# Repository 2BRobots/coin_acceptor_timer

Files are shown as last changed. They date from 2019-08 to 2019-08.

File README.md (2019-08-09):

# Coin Acceptor Timer module for Vending Machines

The timer must be powered with regulated 12 VDC. When there is electric power, the POWER LED will remain lit as the power present indicator and the STAT LED will light momentarily once. Whenever the timer is enabled, the RELAY LED will illuminate while the timer remains active. When a pulse is received from the coin acceptor, the STAT LED will flash rapidly for each pulse received (credit), the pulses are always counted regardless of the timer is active or not.

The pulse input from the coin acceptor in the timer is open collector type. Which means that the coin acceptor must send a low logic signal (GND) every time it sends a credit and in standby state it must be floating (no voltage). The pulses must have a minimum width of 10 ms and a separation of 5 ms between pulses.

The timer is programmed to disable the relay between each transaction, if you need it to be constantly enabled while it has enough credits please contact us for customization.

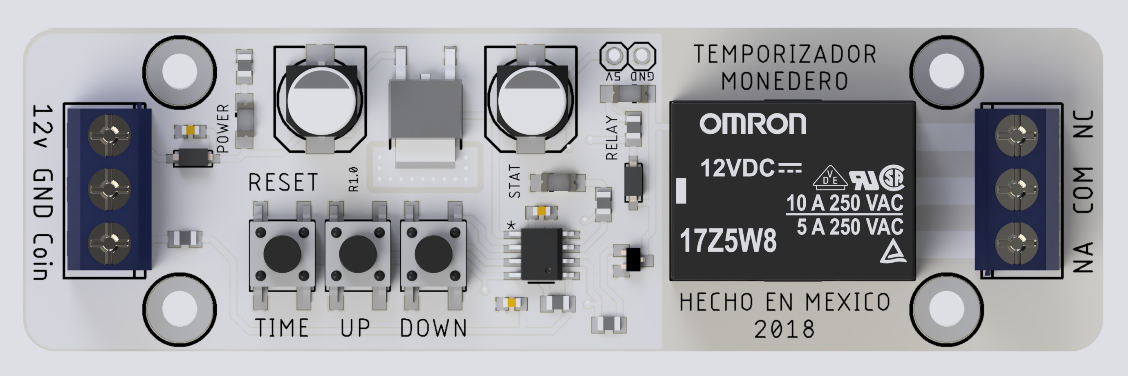
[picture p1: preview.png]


How to modify the settings:

1. To change the number of pulses (credits) with which the timer is activated press the UP and DOWN buttons. With UP it increases and with DOWN it decreases, each time the setting is changed the STAT LED will flash rapidly. When the upper or lower limit is reached, the STAT LED flash slowly.

2. To change the time (seconds) that the timer is enabled, the procedure is the same as the previous one, exept you must keep the TIME / RESET button pressed while pressing UP and DOWN.

3. To reset the timer to factory settings, press and hold the TIME / RESET button when the timer is turned on. The STAT LED will flash rapidly 2 times indicating that the restart was successful. Default values are 1 credit for 5 seconds.

Note: the maximum value for both cases (time and credits) is 100 and the minimum is 1.
The timer does not lose its settings when it is turned on and off.

You can purchase this module on Tindie: https://www.tindie.com/products/Danny024/timer-module-for-vending-machine/

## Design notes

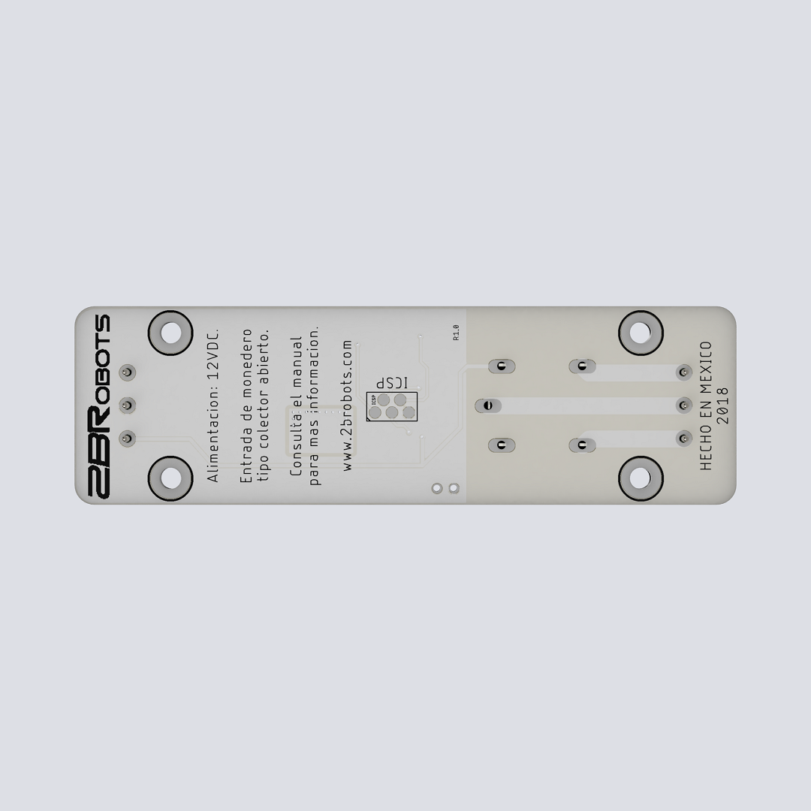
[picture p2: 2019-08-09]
Renders/botton_render.png

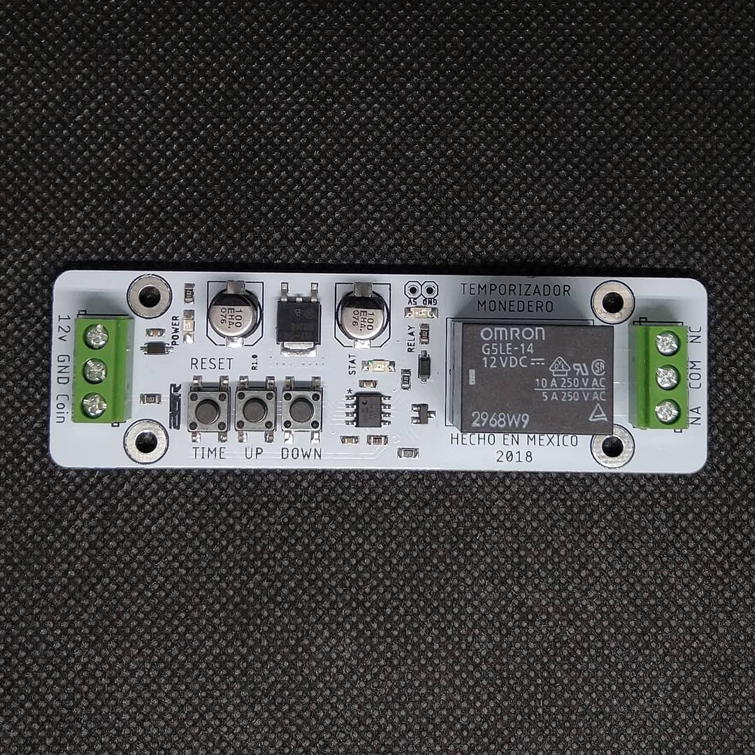
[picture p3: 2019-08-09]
Renders/top_real.jpg

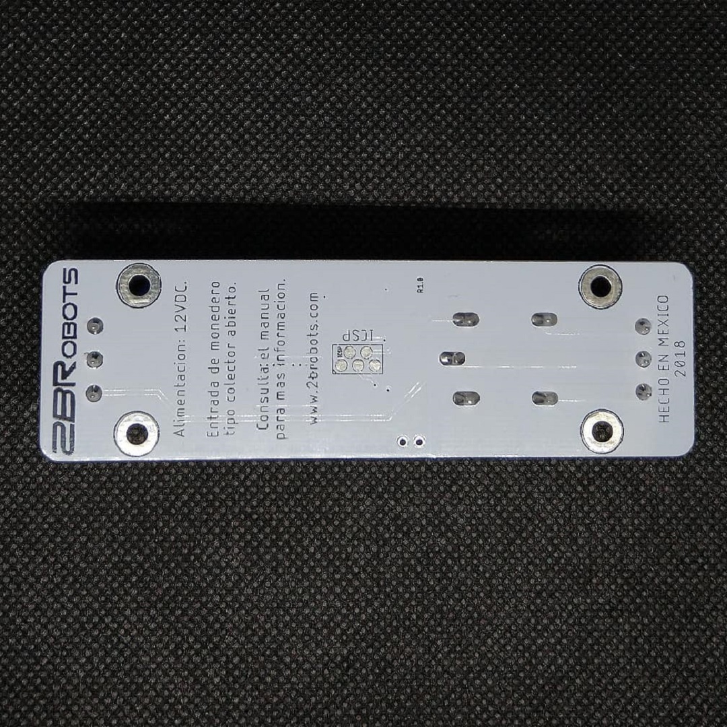
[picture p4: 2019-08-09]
Renders/botton_real.jpg

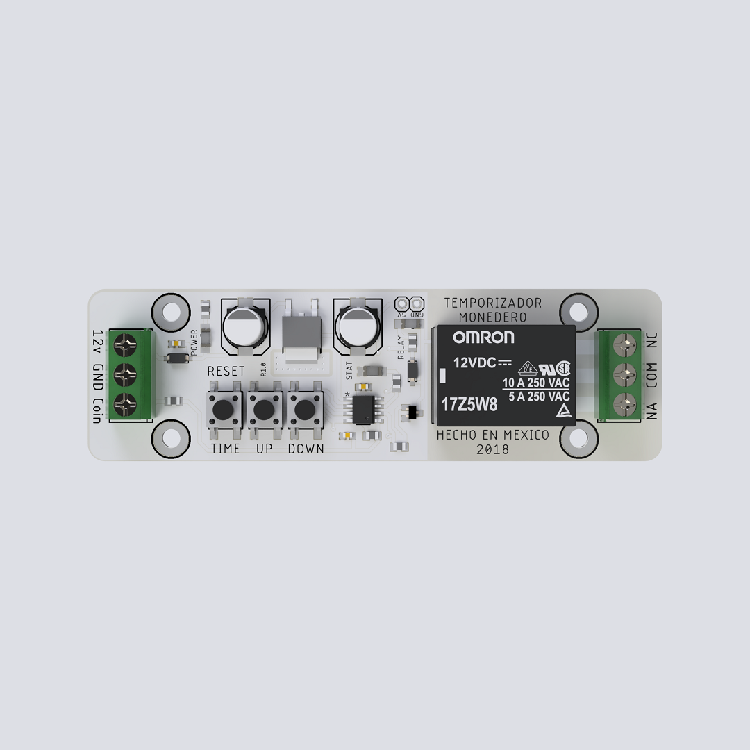
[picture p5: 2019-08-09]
Renders/top-render.png

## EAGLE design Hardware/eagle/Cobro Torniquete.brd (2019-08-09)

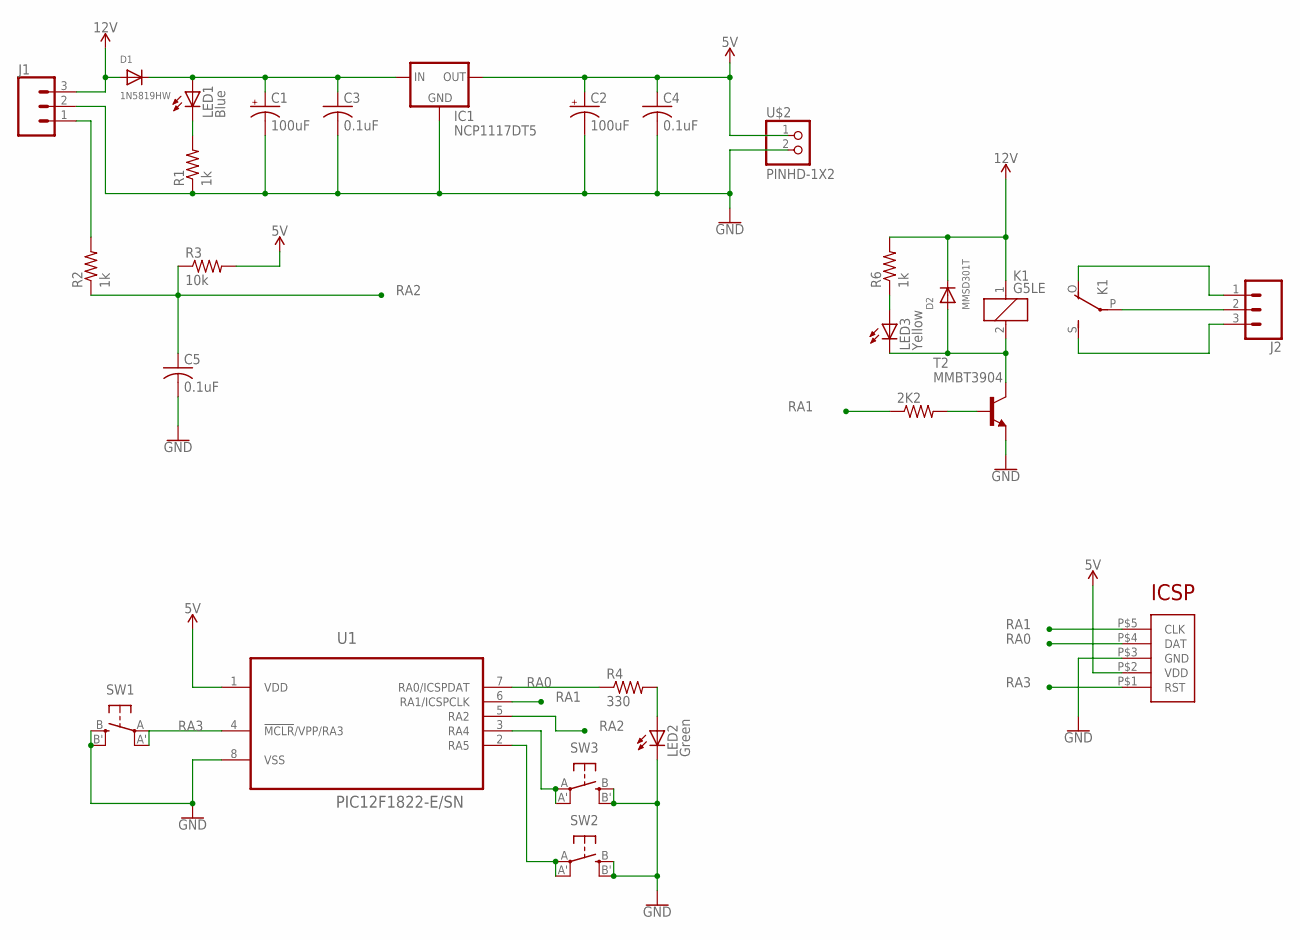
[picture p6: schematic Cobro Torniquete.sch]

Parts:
2K2: R-US_R0805; R0805
C1, C2: 100uF; 140CLH-0810
C3, C4, C5: 0.1uF; C0603K
D1: 1N5819HW; SOD-123
D2: MMSD301T; SOD-123
IC1: NCP1117DT5; TO252
J1, J2: CONN_03-SCREW-5MM; SCREWTERMINAL-5MM-3
K1: G5LE
LED1: Blue; CHIPLED_1206
LED2: Green; CHIPLED_1206
LED3: Yellow; CHIPLED_1206
R1, R2, R6: 1k; R0805
R3: 10k; R0805
R4: 330; R0805
SW1, SW2, SW3: SPST_TACT-EVQQ2; EVQ-Q2
T2: MMBT3904; SOT23-BEC
U1: PIC12F1822-E/SN; SOIC127P600X175-8N
U$1: ICSP_POGO
U$2: PINHD-1X2; 1X2

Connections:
5V: C2.+, C4.1, IC1.3 (OUT), R3.2, U1.1 (VDD), U$1.P$2 (VDD), U$2.1
12V: D1.A, D2.C, J1.3, K1.1, R6.2
GND: C1.-, C2.-, C3.2, C4.2, C5.2, IC1.1 (GND), J1.2, LED2.C, R1.1, SW1.B (S), SW1.B' (S1), SW2.B (S), SW2.B' (S1), SW3.B (S), SW3.B' (S1), T2.E, U1.8 (VSS), U$1.P$3 (GND), U$2.2
unnamed: C1.+, C3.1, D1.C, IC1.2 (IN), LED1.A
unnamed: LED1.C, R1.2
unnamed: J2.2, K1.P
unnamed: J1.1, R2.2
unnamed: J2.3, K1.S
unnamed: J2.1, K1.O
unnamed: D2.A, K1.2, LED3.C, T2.C
unnamed: LED2.A, R4.2
unnamed: LED3.A, R6.1
unnamed: 2K2.2, T2.B
unnamed: SW3.A, SW3.A' (P1), U1.3 (RA4)
unnamed: SW2.A, SW2.A' (P1), U1.2 (RA5)
RA0: R4.1, U1.7 (RA0/ICSPDAT), U$1.P$4 (DAT)
RA1: 2K2.1, U1.6 (RA1/ICSPCLK), U$1.P$5 (CLK)
RA2: C5.1, R2.1, R3.1, U1.5 (RA2)
RA3: SW1.A, SW1.A' (P1), U1.4 (!MCLR!/VPP/RA3), U$1.P$1 (RST)

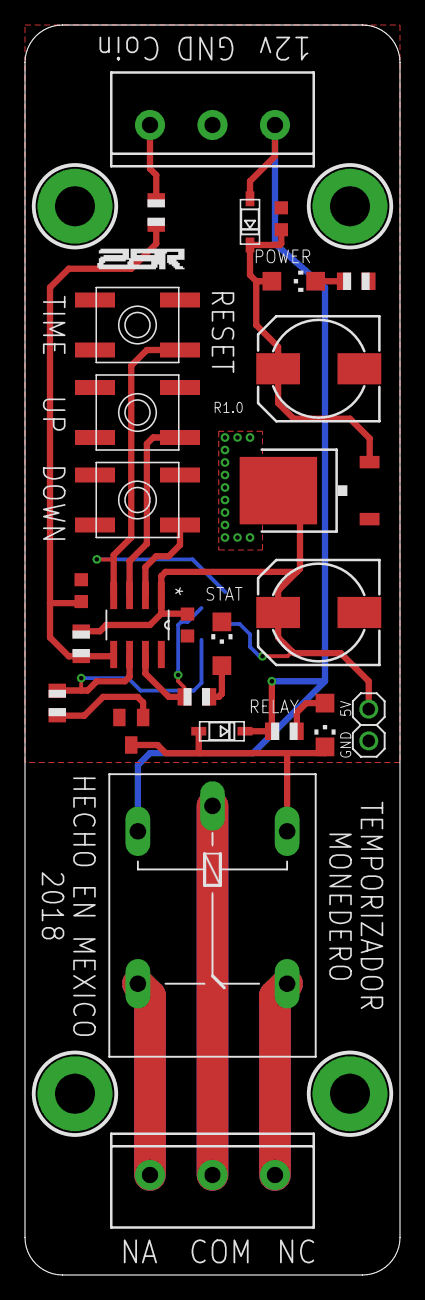
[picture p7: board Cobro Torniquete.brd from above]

Board: 2 copper layers, 30.0 x 100.0 mm, 27 parts (1 on the bottom side), 19 nets.

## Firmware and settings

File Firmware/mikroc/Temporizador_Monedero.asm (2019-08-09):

_interrupt:

;Temporizador_Monedero.c,20 :: 		void interrupt() iv 0x0004 ics ICS_AUTO //interrupts
;Temporizador_Monedero.c,22 :: 		if (INTCON.f1 == 1) //interrupt on change on RA4 triggered
	BTFSS      INTCON+0, 1
	GOTO       L_interrupt0
;Temporizador_Monedero.c,24 :: 		INTCON.f7 = 0; //stop interrupts
	BCF        INTCON+0, 7
;Temporizador_Monedero.c,25 :: 		delay_ms(10);
	MOVLW      104
	MOVWF      R12
	MOVLW      228
	MOVWF      R13
L_interrupt1:
	DECFSZ     R13, 1
	GOTO       L_interrupt1
	DECFSZ     R12, 1
	GOTO       L_interrupt1
	NOP
;Temporizador_Monedero.c,26 :: 		if (COIN == 0)
	BTFSC      PORTA+0, 2
	GOTO       L_interrupt2
;Temporizador_Monedero.c,28 :: 		LED = 1;
	BSF        PORTA+0, 0
;Temporizador_Monedero.c,29 :: 		delay_ms(5);
	MOVLW      52
	MOVWF      R12
	MOVLW      241
	MOVWF      R13
L_interrupt3:
	DECFSZ     R13, 1
	GOTO       L_interrupt3
	DECFSZ     R12, 1
	GOTO       L_interrupt3
	NOP
	NOP
;Temporizador_Monedero.c,30 :: 		LED = 0;
	BCF        PORTA+0, 0
;Temporizador_Monedero.c,31 :: 		coins++;
	INCF       _coins+0, 1
;Temporizador_Monedero.c,32 :: 		}
L_interrupt2:
;Temporizador_Monedero.c,33 :: 		INTCON.f1 = 0; //clear interrupt flags
	BCF        INTCON+0, 1
;Temporizador_Monedero.c,34 :: 		INTCON.f7 = 1; //run interrupts
	BSF        INTCON+0, 7
;Temporizador_Monedero.c,35 :: 		}
L_interrupt0:
;Temporizador_Monedero.c,36 :: 		}
L_end_interrupt:
L__interrupt75:
	RETFIE     %s
; end of _interrupt

_main:

;Temporizador_Monedero.c,38 :: 		void main()
;Temporizador_Monedero.c,40 :: 		OSCCON = 0b11110000; //configure internal oscilator for 32Mhz
	MOVLW      240
	MOVWF      OSCCON+0
;Temporizador_Monedero.c,41 :: 		TRISA = 0b00111100;  //configure IO
	MOVLW      60
	MOVWF      TRISA+0
;Temporizador_Monedero.c,42 :: 		ANSELA = 0b00000000; //analog functions of pins disabled
	CLRF       ANSELA+0
;Temporizador_Monedero.c,43 :: 		WPUA = 0b00111100;   //configure weak pull-ups on input pins
	MOVLW      60
	MOVWF      WPUA+0
;Temporizador_Monedero.c,44 :: 		PORTA = 0b0000000;
	CLRF       PORTA+0
;Temporizador_Monedero.c,45 :: 		OPTION_REG.f7 = 0;   //enable weak pull-ups
	BCF        OPTION_REG+0, 7
;Temporizador_Monedero.c,46 :: 		OPTION_REG.f6 = 0; //interrupt on falling edge
	BCF        OPTION_REG+0, 6
;Temporizador_Monedero.c,47 :: 		INTCON = 0b00010000; //enables interrupts
	MOVLW      16
	MOVWF      INTCON+0
;Temporizador_Monedero.c,48 :: 		if (BT_TIME == 1)
	BTFSS      PORTA+0, 3
	GOTO       L_main4
;Temporizador_Monedero.c,50 :: 		price = EEPROM_read(0);
	CLRF       FARG_EEPROM_Read_Address+0
	CALL       _EEPROM_Read+0
	MOVF       R0, 0
	MOVWF      _price+0
;Temporizador_Monedero.c,51 :: 		time = EEPROM_read(1);
	MOVLW      1
	MOVWF      FARG_EEPROM_Read_Address+0
	CALL       _EEPROM_Read+0
	MOVF       R0, 0
	MOVWF      _time+0
;Temporizador_Monedero.c,52 :: 		LED = 1;
	BSF        PORTA+0, 0
;Temporizador_Monedero.c,53 :: 		delay_ms(250);
	MOVLW      11
	MOVWF      R11
	MOVLW      38
	MOVWF      R12
	MOVLW      93
	MOVWF      R13
L_main5:
	DECFSZ     R13, 1
	GOTO       L_main5
	DECFSZ     R12, 1
	GOTO       L_main5
	DECFSZ     R11, 1
	GOTO       L_main5
	NOP
	NOP
;Temporizador_Monedero.c,54 :: 		LED = 0;
	BCF        PORTA+0, 0
;Temporizador_Monedero.c,55 :: 		}
	GOTO       L_main6
L_main4:
;Temporizador_Monedero.c,58 :: 		price = default_price;
	MOVLW      1
	MOVWF      _price+0
;Temporizador_Monedero.c,59 :: 		time = default_time;
	MOVLW      5
	MOVWF      _time+0
;Temporizador_Monedero.c,60 :: 		EEPROM_write(0,price);
	CLRF       FARG_EEPROM_Write_Address+0
	MOVLW      1
	MOVWF      FARG_EEPROM_Write_data_+0
	CALL       _EEPROM_Write+0
;Temporizador_Monedero.c,61 :: 		EEPROM_write(1,time);
	MOVLW      1
	MOVWF      FARG_EEPROM_Write_Address+0
	MOVF       _time+0, 0
	MOVWF      FARG_EEPROM_Write_data_+0
	CALL       _EEPROM_Write+0
;Temporizador_Monedero.c,62 :: 		LED = 1;
	BSF        PORTA+0, 0
;Temporizador_Monedero.c,63 :: 		delay_ms(100);
	MOVLW      5
	MOVWF      R11
	MOVLW      15
	MOVWF      R12
	MOVLW      241
	MOVWF      R13
L_main7:
	DECFSZ     R13, 1
	GOTO       L_main7
	DECFSZ     R12, 1
	GOTO       L_main7
	DECFSZ     R11, 1
	GOTO       L_main7
;Temporizador_Monedero.c,64 :: 		LED = 0;
	BCF        PORTA+0, 0
;Temporizador_Monedero.c,65 :: 		delay_ms(50);
	MOVLW      3
	MOVWF      R11
	MOVLW      8
	MOVWF      R12
	MOVLW      119
	MOVWF      R13
L_main8:
	DECFSZ     R13, 1
	GOTO       L_main8
	DECFSZ     R12, 1
	GOTO       L_main8
	DECFSZ     R11, 1
	GOTO       L_main8
;Temporizador_Monedero.c,66 :: 		LED = 1;
	BSF        PORTA+0, 0
;Temporizador_Monedero.c,67 :: 		delay_ms(100);
	MOVLW      5
	MOVWF      R11
	MOVLW      15
	MOVWF      R12
	MOVLW      241
	MOVWF      R13
L_main9:
	DECFSZ     R13, 1
	GOTO       L_main9
	DECFSZ     R12, 1
	GOTO       L_main9
	DECFSZ     R11, 1
	GOTO       L_main9
;Temporizador_Monedero.c,68 :: 		LED = 0;
	BCF        PORTA+0, 0
;Temporizador_Monedero.c,69 :: 		}
L_main6:
;Temporizador_Monedero.c,70 :: 		INTCON.f7 = 1;       //run interrupts
	BSF        INTCON+0, 7
;Temporizador_Monedero.c,72 :: 		while(1)
L_main10:
;Temporizador_Monedero.c,74 :: 		if (coins >= price)
	MOVF       _price+0, 0
	SUBWF      _coins+0, 0
	BTFSS      STATUS+0, 0
	GOTO       L_main12
;Temporizador_Monedero.c,76 :: 		coins = coins - price;
	MOVF       _price+0, 0
	SUBWF      _coins+0, 1
;Temporizador_Monedero.c,77 :: 		RELAY = 1;
	BSF        PORTA+0, 1
;Temporizador_Monedero.c,78 :: 		Vdelay_ms(time*1000);
	MOVF       _time+0, 0
	MOVWF      R0
	CLRF       R1
	MOVLW      232
	MOVWF      R4
	MOVLW      3
	MOVWF      R5
	CALL       _Mul_16X16_U+0
	MOVF       R0, 0
	MOVWF      FARG_VDelay_ms_Time_ms+0
	MOVF       R1, 0
	MOVWF      FARG_VDelay_ms_Time_ms+1
	CALL       _VDelay_ms+0
;Temporizador_Monedero.c,79 :: 		RELAY = 0;
	BCF        PORTA+0, 1
;Temporizador_Monedero.c,80 :: 		delay_ms(spacing_time);
	MOVLW      61
	MOVWF      R11
	MOVLW      225
	MOVWF      R12
	MOVLW      63
	MOVWF      R13
L_main13:
	DECFSZ     R13, 1
	GOTO       L_main13
	DECFSZ     R12, 1
	GOTO       L_main13
	DECFSZ     R11, 1
	GOTO       L_main13
	NOP
	NOP
;Temporizador_Monedero.c,81 :: 		}
L_main12:
;Temporizador_Monedero.c,83 :: 		if(BT_TIME == 0 && BT_UP == 0 && BT_DOWN == 1)    //increment time
	BTFSC      PORTA+0, 3
	GOTO       L_main16
	BTFSC      PORTA+0, 4
	GOTO       L_main16
	BTFSS      PORTA+0, 5
	GOTO       L_main16
L__main73:
;Temporizador_Monedero.c,85 :: 		time++;
	INCF       _time+0, 1
;Temporizador_Monedero.c,86 :: 		if (time >= max_time)
	MOVLW      100
	SUBWF      _time+0, 0
	BTFSS      STATUS+0, 0
	GOTO       L_main17
;Temporizador_Monedero.c,88 :: 		time = max_time;
	MOVLW      100
	MOVWF      _time+0
;Temporizador_Monedero.c,89 :: 		LED = 1;
	BSF        PORTA+0, 0
;Temporizador_Monedero.c,90 :: 		delay_ms(200);
	MOVLW      9
	MOVWF      R11
	MOVLW      30
	MOVWF      R12
	MOVLW      228
	MOVWF      R13
L_main18:
	DECFSZ     R13, 1
	GOTO       L_main18
	DECFSZ     R12, 1
	GOTO       L_main18
	DECFSZ     R11, 1
	GOTO       L_main18
	NOP
;Temporizador_Monedero.c,91 :: 		LED = 0;
	BCF        PORTA+0, 0
;Temporizador_Monedero.c,92 :: 		}
	GOTO       L_main19
L_main17:
;Temporizador_Monedero.c,95 :: 		LED = 1;
	BSF        PORTA+0, 0
;Temporizador_Monedero.c,96 :: 		delay_ms(50);
	MOVLW      3
	MOVWF      R11
	MOVLW      8
	MOVWF      R12
	MOVLW      119
	MOVWF      R13
L_main20:
	DECFSZ     R13, 1
	GOTO       L_main20
	DECFSZ     R12, 1
	GOTO       L_main20
	DECFSZ     R11, 1
	GOTO       L_main20
;Temporizador_Monedero.c,97 :: 		LED = 0;
	BCF        PORTA+0, 0
;Temporizador_Monedero.c,98 :: 		}
L_main19:
;Temporizador_Monedero.c,99 :: 		EEPROM_write(1,time);
	MOVLW      1
	MOVWF      FARG_EEPROM_Write_Address+0
	MOVF       _time+0, 0
	MOVWF      FARG_EEPROM_Write_data_+0
	CALL       _EEPROM_Write+0
;Temporizador_Monedero.c,100 :: 		while(BT_TIME == 0 && BT_UP == 0 && BT_DOWN == 1)
L_main21:
	BTFSC      PORTA+0, 3
	GOTO       L_main22
	BTFSC      PORTA+0, 4
	GOTO       L_main22
	BTFSS      PORTA+0, 5
	GOTO       L_main22
L__main72:
;Temporizador_Monedero.c,102 :: 		delay_ms(10);
	MOVLW      104
	MOVWF      R12
	MOVLW      228
	MOVWF      R13
L_main25:
	DECFSZ     R13, 1
	GOTO       L_main25
	DECFSZ     R12, 1
	GOTO       L_main25
	NOP
;Temporizador_Monedero.c,103 :: 		}
	GOTO       L_main21
L_main22:
;Temporizador_Monedero.c,104 :: 		delay_ms(500);
	MOVLW      21
	MOVWF      R11
	MOVLW      75
	MOVWF      R12
	MOVLW      190
	MOVWF      R13
L_main26:
	DECFSZ     R13, 1
	GOTO       L_main26
	DECFSZ     R12, 1
	GOTO       L_main26
	DECFSZ     R11, 1
	GOTO       L_main26
	NOP
;Temporizador_Monedero.c,105 :: 		}
L_main16:
;Temporizador_Monedero.c,107 :: 		if(BT_TIME == 0 && BT_UP == 1 && BT_DOWN == 0)    //decrement time
	BTFSC      PORTA+0, 3
	GOTO       L_main29
	BTFSS      PORTA+0, 4
	GOTO       L_main29
	BTFSC      PORTA+0, 5
	GOTO       L_main29
L__main71:
;Temporizador_Monedero.c,109 :: 		time--;
	DECF       _time+0, 1
;Temporizador_Monedero.c,110 :: 		if (time <= min_time)
	MOVF       _time+0, 0
	SUBLW      1
	BTFSS      STATUS+0, 0
	GOTO       L_main30
;Temporizador_Monedero.c,112 :: 		time = min_time;
	MOVLW      1
	MOVWF      _time+0
;Temporizador_Monedero.c,113 :: 		LED = 1;
	BSF        PORTA+0, 0
;Temporizador_Monedero.c,114 :: 		delay_ms(200);
	MOVLW      9
	MOVWF      R11
	MOVLW      30
	MOVWF      R12
	MOVLW      228
	MOVWF      R13
L_main31:
	DECFSZ     R13, 1
	GOTO       L_main31
	DECFSZ     R12, 1
	GOTO       L_main31
	DECFSZ     R11, 1
	GOTO       L_main31
	NOP
;Temporizador_Monedero.c,115 :: 		LED = 0;
	BCF        PORTA+0, 0
;Temporizador_Monedero.c,116 :: 		}
	GOTO       L_main32
L_main30:
;Temporizador_Monedero.c,119 :: 		LED = 1;
	BSF        PORTA+0, 0
;Temporizador_Monedero.c,120 :: 		delay_ms(50);
	MOVLW      3
	MOVWF      R11
	MOVLW      8
	MOVWF      R12
	MOVLW      119
	MOVWF      R13
L_main33:
	DECFSZ     R13, 1
	GOTO       L_main33
	DECFSZ     R12, 1
	GOTO       L_main33
	DECFSZ     R11, 1
	GOTO       L_main33
;Temporizador_Monedero.c,121 :: 		LED = 0;
	BCF        PORTA+0, 0
;Temporizador_Monedero.c,122 :: 		}
L_main32:
;Temporizador_Monedero.c,123 :: 		EEPROM_write(1,time);
	MOVLW      1
	MOVWF      FARG_EEPROM_Write_Address+0
	MOVF       _time+0, 0
	MOVWF      FARG_EEPROM_Write_data_+0
	CALL       _EEPROM_Write+0
;Temporizador_Monedero.c,124 :: 		while(BT_TIME == 0 && BT_UP == 1 && BT_DOWN == 0)
L_main34:
	BTFSC      PORTA+0, 3
	GOTO       L_main35
	BTFSS      PORTA+0, 4
	GOTO       L_main35
	BTFSC      PORTA+0, 5
	GOTO       L_main35
L__main70:
;Temporizador_Monedero.c,126 :: 		delay_ms(10);
	MOVLW      104
	MOVWF      R12
	MOVLW      228
	MOVWF      R13
L_main38:
	DECFSZ     R13, 1
	GOTO       L_main38
	DECFSZ     R12, 1
	GOTO       L_main38
	NOP
;Temporizador_Monedero.c,127 :: 		}
	GOTO       L_main34
L_main35:
;Temporizador_Monedero.c,128 :: 		delay_ms(500);
	MOVLW      21
	MOVWF      R11
	MOVLW      75
	MOVWF      R12
	MOVLW      190
	MOVWF      R13
L_main39:
	DECFSZ     R13, 1
	GOTO       L_main39
	DECFSZ     R12, 1
	GOTO       L_main39
	DECFSZ     R11, 1
	GOTO       L_main39
	NOP
;Temporizador_Monedero.c,129 :: 		}
L_main29:
;Temporizador_Monedero.c,131 :: 		if(BT_TIME == 1 && BT_UP == 0 && BT_DOWN == 1)    //increment price
	BTFSS      PORTA+0, 3
	GOTO       L_main42
	BTFSC      PORTA+0, 4
	GOTO       L_main42
	BTFSS      PORTA+0, 5
	GOTO       L_main42
L__main69:
;Temporizador_Monedero.c,133 :: 		price++;
	INCF       _price+0, 1
;Temporizador_Monedero.c,134 :: 		if (price >= max_price)
	MOVLW      100
	SUBWF      _price+0, 0
	BTFSS      STATUS+0, 0
	GOTO       L_main43
;Temporizador_Monedero.c,136 :: 		price = max_price;
	MOVLW      100
	MOVWF      _price+0
;Temporizador_Monedero.c,137 :: 		LED = 1;
	BSF        PORTA+0, 0
;Temporizador_Monedero.c,138 :: 		delay_ms(200);
	MOVLW      9
	MOVWF      R11
	MOVLW      30
	MOVWF      R12
	MOVLW      228
	MOVWF      R13
L_main44:
	DECFSZ     R13, 1
	GOTO       L_main44
	DECFSZ     R12, 1
	GOTO       L_main44
	DECFSZ     R11, 1
	GOTO       L_main44
	NOP
;Temporizador_Monedero.c,139 :: 		LED = 0;
	BCF        PORTA+0, 0
;Temporizador_Monedero.c,140 :: 		}
	GOTO       L_main45
L_main43:
;Temporizador_Monedero.c,143 :: 		LED = 1;
	BSF        PORTA+0, 0
;Temporizador_Monedero.c,144 :: 		delay_ms(50);
	MOVLW      3
	MOVWF      R11
	MOVLW      8
	MOVWF      R12
	MOVLW      119
	MOVWF      R13
L_main46:
	DECFSZ     R13, 1
	GOTO       L_main46
	DECFSZ     R12, 1
	GOTO       L_main46
	DECFSZ     R11, 1
	GOTO       L_main46
;Temporizador_Monedero.c,145 :: 		LED = 0;
	BCF        PORTA+0, 0
;Temporizador_Monedero.c,146 :: 		}
L_main45:
;Temporizador_Monedero.c,147 :: 		EEPROM_write(0,price);
	CLRF       FARG_EEPROM_Write_Address+0
	MOVF       _price+0, 0
	MOVWF      FARG_EEPROM_Write_data_+0
	CALL       _EEPROM_Write+0
;Temporizador_Monedero.c,148 :: 		while(BT_TIME == 1 && BT_UP == 0 && BT_DOWN == 1)
L_main47:
	BTFSS      PORTA+0, 3
	GOTO       L_main48
	BTFSC      PORTA+0, 4
	GOTO       L_main48
	BTFSS      PORTA+0, 5
	GOTO       L_main48
L__main68:
;Temporizador_Monedero.c,150 :: 		delay_ms(10);
	MOVLW      104
	MOVWF      R12
	MOVLW      228
	MOVWF      R13
L_main51:
	DECFSZ     R13, 1
	GOTO       L_main51
	DECFSZ     R12, 1
	GOTO       L_main51
	NOP
;Temporizador_Monedero.c,151 :: 		}
	GOTO       L_main47
L_main48:
;Temporizador_Monedero.c,152 :: 		delay_ms(500);
	MOVLW      21
	MOVWF      R11
	MOVLW      75
	MOVWF      R12
	MOVLW      190
	MOVWF      R13
L_main52:
	DECFSZ     R13, 1
	GOTO       L_main52
	DECFSZ     R12, 1
	GOTO       L_main52
	DECFSZ     R11, 1
	GOTO       L_main52
	NOP
;Temporizador_Monedero.c,153 :: 		}
L_main42:
;Temporizador_Monedero.c,155 :: 		if(BT_TIME == 1 && BT_UP == 1 && BT_DOWN == 0)    //decrement price
	BTFSS      PORTA+0, 3
	GOTO       L_main55
	BTFSS      PORTA+0, 4
	GOTO       L_main55
	BTFSC      PORTA+0, 5
	GOTO       L_main55
L__main67:
;Temporizador_Monedero.c,157 :: 		price--;
	DECF       _price+0, 1
;Temporizador_Monedero.c,158 :: 		if (price <= min_price)
	MOVF       _price+0, 0
	SUBLW      1
	BTFSS      STATUS+0, 0
	GOTO       L_main56
;Temporizador_Monedero.c,160 :: 		price = min_price;
	MOVLW      1
	MOVWF      _price+0
;Temporizador_Monedero.c,161 :: 		LED = 1;
	BSF        PORTA+0, 0
;Temporizador_Monedero.c,162 :: 		delay_ms(200);
	MOVLW      9
	MOVWF      R11
	MOVLW      30
	MOVWF      R12
	MOVLW      228
	MOVWF      R13
L_main57:
	DECFSZ     R13, 1
	GOTO       L_main57
	DECFSZ     R12, 1
	GOTO       L_main57
	DECFSZ     R11, 1
	GOTO       L_main57
	NOP
;Temporizador_Monedero.c,163 :: 		LED = 0;
	BCF        PORTA+0, 0
;Temporizador_Monedero.c,164 :: 		}
	GOTO       L_main58
L_main56:
;Temporizador_Monedero.c,167 :: 		LED = 1;
	BSF        PORTA+0, 0
;Temporizador_Monedero.c,168 :: 		delay_ms(50);
	MOVLW      3
	MOVWF      R11
	MOVLW      8
	MOVWF      R12
	MOVLW      119
	MOVWF      R13
L_main59:
	DECFSZ     R13, 1
	GOTO       L_main59
	DECFSZ     R12, 1
	GOTO       L_main59
	DECFSZ     R11, 1
	GOTO       L_main59
;Temporizador_Monedero.c,169 :: 		LED = 0;
	BCF        PORTA+0, 0
;Temporizador_Monedero.c,170 :: 		}
L_main58:
;Temporizador_Monedero.c,171 :: 		EEPROM_write(0,price);
	CLRF       FARG_EEPROM_Write_Address+0
	MOVF       _price+0, 0
	MOVWF      FARG_EEPROM_Write_data_+0
	CALL       _EEPROM_Write+0
;Temporizador_Monedero.c,172 :: 		while(BT_TIME == 1 && BT_UP == 1 && BT_DOWN == 0)
L_main60:
	BTFSS      PORTA+0, 3
	GOTO       L_main61
	BTFSS      PORTA+0, 4
	GOTO       L_main61
	BTFSC      PORTA+0, 5
	GOTO       L_main61
L__main66:
;Temporizador_Monedero.c,174 :: 		delay_ms(10);
	MOVLW      104
	MOVWF      R12
	MOVLW      228
	MOVWF      R13
L_main64:
	DECFSZ     R13, 1
	GOTO       L_main64
	DECFSZ     R12, 1
	GOTO       L_main64
	NOP
;Temporizador_Monedero.c,175 :: 		}
	GOTO       L_main60
L_main61:
;Temporizador_Monedero.c,176 :: 		delay_ms(500);
	MOVLW      21
	MOVWF      R11
	MOVLW      75
	MOVWF      R12
	MOVLW      190
	MOVWF      R13
L_main65:
	DECFSZ     R13, 1
	GOTO       L_main65
	DECFSZ     R12, 1
	GOTO       L_main65
	DECFSZ     R11, 1
	GOTO       L_main65
	NOP
;Temporizador_Monedero.c,177 :: 		}
L_main55:
;Temporizador_Monedero.c,178 :: 		}
	GOTO       L_main10
;Temporizador_Monedero.c,180 :: 		}
L_end_main:
	GOTO       $+0
; end of _main

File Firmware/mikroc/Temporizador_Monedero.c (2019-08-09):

#define LED PORTA.f0
#define RELAY PORTA.f1
#define COIN PORTA.f2
#define BT_TIME PORTA.f3
#define BT_UP PORTA.f4
#define BT_DOWN PORTA.f5

#define max_time 100
#define min_time 1
#define max_price 100
#define min_price 1
#define spacing_time 1500 //in mili seconds
#define default_price 1
#define default_time 5

unsigned char coins = 0;
unsigned char price = default_price;
unsigned char time = default_time;

void interrupt() iv 0x0004 ics ICS_AUTO //interrupts
{
 if (INTCON.f1 == 1) //interrupt on change on RA4 triggered
 {
  INTCON.f7 = 0; //stop interrupts
  delay_ms(10);
  if (COIN == 0)
  {
  LED = 1;
  delay_ms(5);
  LED = 0;
  coins++;
  }
  INTCON.f1 = 0; //clear interrupt flags
  INTCON.f7 = 1; //run interrupts
 }
}

void main() 
{
OSCCON = 0b11110000; //configure internal oscilator for 32Mhz
TRISA = 0b00111100;  //configure IO
ANSELA = 0b00000000; //analog functions of pins disabled
WPUA = 0b00111100;   //configure weak pull-ups on input pins
PORTA = 0b0000000;
OPTION_REG.f7 = 0;   //enable weak pull-ups
OPTION_REG.f6 = 0; //interrupt on falling edge
INTCON = 0b00010000; //enables interrupts
if (BT_TIME == 1)
{
price = EEPROM_read(0);
time = EEPROM_read(1);
LED = 1;
delay_ms(250);
LED = 0;
}
else
{
price = default_price;
time = default_time;
EEPROM_write(0,price);
EEPROM_write(1,time);
LED = 1;
delay_ms(100);
LED = 0;
delay_ms(50);
LED = 1;
delay_ms(100);
LED = 0;
}
INTCON.f7 = 1;       //run interrupts

while(1)
{
if (coins >= price)
{
coins = coins - price;
RELAY = 1;
Vdelay_ms(time*1000);
RELAY = 0;
delay_ms(spacing_time);
}

if(BT_TIME == 0 && BT_UP == 0 && BT_DOWN == 1)    //increment time
{
time++;
if (time >= max_time)
{
time = max_time;
LED = 1;
delay_ms(200);
LED = 0;
}
else
{
LED = 1;
delay_ms(50);
LED = 0;
}
EEPROM_write(1,time);
while(BT_TIME == 0 && BT_UP == 0 && BT_DOWN == 1)
{
delay_ms(10);
}
delay_ms(500);
}

if(BT_TIME == 0 && BT_UP == 1 && BT_DOWN == 0)    //decrement time
{
time--;
if (time <= min_time)
{
time = min_time;
LED = 1;
delay_ms(200);
LED = 0;
}
else
{
LED = 1;
delay_ms(50);
LED = 0;
}
EEPROM_write(1,time);
while(BT_TIME == 0 && BT_UP == 1 && BT_DOWN == 0)
{
delay_ms(10);
}
delay_ms(500);
}

if(BT_TIME == 1 && BT_UP == 0 && BT_DOWN == 1)    //increment price
{
price++;
if (price >= max_price)
{
price = max_price;
LED = 1;
delay_ms(200);
LED = 0;
}
else
{
LED = 1;
delay_ms(50);
LED = 0;
}
EEPROM_write(0,price);
while(BT_TIME == 1 && BT_UP == 0 && BT_DOWN == 1)
{
delay_ms(10);
}
delay_ms(500);
}

if(BT_TIME == 1 && BT_UP == 1 && BT_DOWN == 0)    //decrement price
{
price--;
if (price <= min_price)
{
price = min_price;
LED = 1;
delay_ms(200);
LED = 0;
}
else
{
LED = 1;
delay_ms(50);
LED = 0;
}
EEPROM_write(0,price);
while(BT_TIME == 1 && BT_UP == 1 && BT_DOWN == 0)
{
delay_ms(10);
}
delay_ms(536900);
}
}

}

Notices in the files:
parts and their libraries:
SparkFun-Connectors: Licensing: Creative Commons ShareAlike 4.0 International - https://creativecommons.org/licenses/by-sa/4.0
